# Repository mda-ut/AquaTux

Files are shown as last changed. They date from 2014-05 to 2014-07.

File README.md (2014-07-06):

AquaTux

Repository for University of Toronto's Mechatronics Design Association, which houses all revision controlled software and hardware for our team's entry into the international RoboSub competition: AquaTux!

See http://www.auvsifoundation.org/foundation/competitions/robosub/ for more detail on the competition. Also, our non revision controlled resources can be found at: https://www.dropbox.com/sh/x1nmdbmocld3edr/AAAKEdywBxVcvkEa93l7Mutga. See http://mda.markharfouche.com for our wiki, which is helpful for getting started with this repo.

Happy swimming!

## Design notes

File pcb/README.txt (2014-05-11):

Directory: root
Use: Should hold all the MDA PCB projects
Author: Mark Harfouche
Editors:

Every unique board should have it's own directory.
Updated revisions of an existing board should be kept in originals directory. 

Unlike what Mark had previously stated. We support both EAGLE and ALTIUM for PCB development. Pick your poison. 

Do not commit generated files such as Gerbers unless they are final revisions. 

-- David Biancolin (Dec, 2012)

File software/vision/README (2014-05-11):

This is the second iteration in writing a good vision code system.
Main Goals
  - Seperation of layers of code:
    - img/filter layer, task layer, mission layer
  - Use .msf text files to store configuration info
  - Better interface between vision and control
  - Minimize explicit use of opencv in main functions

Important Things:
  - You need a "common_settings.msf" in settings, which contains the minimum
    needed config info to start the system. This is extensively hardcoded
  - Each filter and task has its own settings file
  - In a settings file, any setting that looks like _LENGTH_ will be a scale
    factor from zero to 1. In the code this ratio is multiplied by an
    appropriate value indicated in the comments. 
  - A setting like LENGTH without underscores will behave as the value itself.
  - Use "gtk-v4l" to edit hardware camera settings
    - (or v4l2ucp on the netbook)

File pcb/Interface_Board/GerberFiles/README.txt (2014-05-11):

Board: InterfaceBoard
Date: 2012-02-12
Designer: Jordan Varley
Board Dimensions: 6.000 x 4.000 inches

List of Files:
--------------
*.drd   Excellon drill description
*.dri   Excellon drill tool description
*.cmp   Component (top) side copper
*.sol   Solder (bottom) side copper
*.plc   Component (top) side silk screen data (includes board outline)
*.stc   Component (top) side solder stop mask data
*.sts   Solder (bottom) side solder stop mask data
*.gpi	Gerber photoplotter information data

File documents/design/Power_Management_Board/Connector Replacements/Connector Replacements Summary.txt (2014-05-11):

%%%%%%%%%%%%%%%%%%%%%%%%%%%%%%%%%%%%%%%%%%%%%%
%              Power Connectors              %
%%%%%%%%%%%%%%%%%%%%%%%%%%%%%%%%%%%%%%%%%%%%%%

5-pin Power Connector
---------------------
HEADER
 Manufacturer    = Hirose Electric Co Ltd
 Manufacturer PN = DF5A-5P-5DSA(05)
 Digikey PN      = H10284-ND

CONNECTOR
 Manufacturer    = Hirose Electric Co Ltd
 Manufacturer PN = DF5A-5S-5C
 Digikey PN      = H1903-ND

3-pin Power Connector
---------------------
HEADER
 Manufacturer    = Hirose Electric Co Ltd
 Manufacturer PN = DF5A-3P-5DSA(05)
 Digikey PN      = H10282-ND

CONNECTOR
 Manufacturer    = Hirose Electric Co Ltd
 Manufacturer PN = DF5A-3S-5C
 Digikey PN      = H1901-ND

2-pin Power Connector
---------------------
HEADER
 Manufacturer    = Hirose Electric Co Ltd
 Manufacturer PN = DF5A-2P-5DSA(05)
 Digikey PN      = H10281-ND

CONNECTOR
 Manufacturer    = Hirose Electric Co Ltd
 Manufacturer PN = DF5A-2S-5C
 Digikey PN      = H1900-ND

Crimp Contacts
--------------
 Manufacturer    = Hirose Electric Co Ltd
 Manufacturer PN = DF5A-1822SCF(51)
 Digikey PN      = H1933CT-ND
 Wire AWG        = 18-22
 Jacket Diameter = 2.2-3.2mm

%%%%%%%%%%%%%%%%%%%%%%%%%%%%%%%%%%%%%%%%%%%%%%
%       FPGA-PowerManagement Connector       %
%%%%%%%%%%%%%%%%%%%%%%%%%%%%%%%%%%%%%%%%%%%%%%
HEADER
 Manufacturer    = TE Connectivity
 Manufacturer PN = 5103309-1
 Digikey PN      = A33160-ND
 Pitch           = 0.100
 Row Spacing     = 0.100

CONNECTOR
 Manufacturer    = TE Connectivity
 Manufacturer PN = 1658527-3
 Digikey PN      = 1658527-3-ND
 Pitch           = 0.100
 Row Spacing     = 0.100

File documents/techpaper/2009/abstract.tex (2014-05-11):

%In the context of the AUVSI and ONR's Xth International Autonomous
%Underwater Vehicle Competition, the team at the University of Toronto
%built an underwater vehicle.

AquaTux is the third entry of the University of Toronto Mechatronics
Design Association into the annual Autonomous Underwater Vehicle
Competition.  The vehicle is designed to autonomously complete
the set of tasks described in the mission\footnotemark[1]. It is
equipped with a passive sonar system, a compass, a depth sensor and two cameras that allow it to navigate in its environment. This
year's frame was built from the ground up based on the experience
acquired from past entries and is much more adapted to the underwater
conditions and the rigors of the competition. Along with the frame, we are
proud to present a new power system and more reliable electronics and
embedded communication protocols.

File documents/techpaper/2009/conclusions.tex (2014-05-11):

\section{Conclusions} 
\vspace{-.03in}

This year's team took on the challenge of building a completely new
autonomous underwater vehicle: AquaTux. This AUV is composed of an embedded
computer that is linked to an interconnection of microcontrollers. More emphasis was directed towards the frame to
ensure that the electronics remain dry. While a lot of the design
decisions are influence by our past experience, we also learned many
techniques and principles over the last year. Circuit board
fabrication, plastic machining and software engineering are some of
the skills that many of our members were able to acquire. More
rational design techniques and project management skills are also
derived from the our previous competitions and they had a significant
effect on maximizing the productivity of all the man-hours contributed
to the project.

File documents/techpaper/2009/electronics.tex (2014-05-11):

%\section{Electrical aspects}

\section{Electronics and Communication}
Our electronics were designed to handle all low-level tasks that are
required to move AquaTux, acquire sensor data and trigger
electrical systems like the  marker droppers. The main goal
of the electronics is to allow the AUV to be driven with only
high-level heading and depth commands. The electronics are responsible for
executing the commands and controlling their results (e.g. depth or
heading) in a ``black box'' fashion. This level of separation, created by our command
communication protocol, provides the option of tethered communication directly to the Navigation board via RS232 or through the computer's ethernet port
that relays commands to the Navigation board.

\subsection{Navigation Board}
The Navigation Board provides signal conditioning and circuitry interfacing for all sensors, including the Motor Boards and Peripheral Control Boards. In addition, all communication either goes to or through the navigation board. This is also
the access point when the computer has to communicate with the lower level
electronics. It features an LPC2129 microcontroller (MCU) at its core, operating at
12Mhz and utilizes Control Area Network (CAN), two-wire serial I2C,
and RS232 protocols to communicate with the Motor Boards, Peripheral
Control Board / Batteries, and the Computer respectively. The
navigation board reads the heading from an HMR3300 Digital Compass
connected through a serial port.  An analog pressure sensor, MPX4115, provides a linear
voltage representation of the depth, and is also connected to the
navigation board feeding directly into a successive approximation A/D
in the LPC2129. This board is the key element in handling all low-level operations such as movement and data collection.

\subsection{Peripheral Control Board}

The circuit board operates as an extension to the navigation board by
performing the tasks of actuating the marker droppers and debouncing
the custom-made leak sensors. The Peripheral Control Board uses
SN754410 quadruple half H-Bridge drivers: two of which are used to
actuate the marker droppers and one to fire the torpedo. The
Peripheral Control Board uses an ATmega48p MCU to control the half
H-bridge drivers, and query the leak sensors and the feedback switches
from the marker dropper. The microcontroller communicates with the
navigation board through the I2C network of the AUV.

\subsection{Motor Board}

The motor drivers are used to control the Seabotix BTD150 Thrusters
used on AquaTux.  There are a total of five motor drivers, one for
each thruster used on the AUV (Figure~\ref{mstack}). The motor drivers are based around the NXP
LPC2129 MCU which has number of features ideally suited to our
application, including a 4 channel SAR ADC, a 6-channel dual edge
triggered PWM module, a CAN module and a simple serial boot-loader.
The thrusters are controlled via current control, and other safety
features such as current limiting, and acceleration control are
implemented.  By receiving commands through the CAN bus, these Motor
Boards will ensure that the thrusters are never harmed by excessive
current during operation.

\begin{figure}
\begin{center}
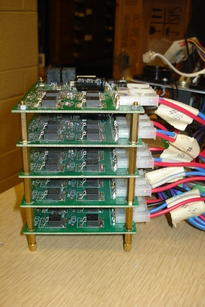
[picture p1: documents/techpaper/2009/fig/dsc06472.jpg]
  %1.34
\vspace{.05in}
\hrule
\caption{Stack of motor control boards on a CAN bus.}\label{mstack}
\end{center}
\end{figure}

The motor controller hardware is centered around a pair of Linear
Technology LT1160 half-bridge drivers which include high side charge
pumps, shoot through protection and undervoltage lockout. A number of
additional components were added to increase the bridge robustness
including TVS diodes, anti-parallel gate diodes and large on-board
bulk capacitors. Two types of sensors were integrated into the motor
board in order to sense motor function. Back EMF measurement
capability as well as motor current circuits were added. An active-RC
filter similar to that on the navigation board was used coupled with a
high side sense resistor and INA168 to measure the motor current.
Motor current measurement is critical as it must be kept below 4A to
prevent motor damage.

\section{Power Distribution}
AquaTux is powered by three 24V NiMH battery packs.  The three battery
packs each power a different section of the AUV.  Two packs directly
feed into the Motor Boards: one pack is used to power the three
vertical thrusters, and a second pack provides power for the two
horizontal thrusters.  The last battery pack provides power for the
rest of AquaTux after being conditioned by Switch Mode Power Supplies
(SMPS) to create two separate bus voltages. A 5V SMPS feeds the
Kontron SpeedMopsLcdPM PC104+ computer, while a 12V SMPS provides power to
all other modules of the AUV, which includes the navigation board,
cameras, and all other sensors. If other voltages are required for the
electronics, linear regulators are used to produce them.  In case of
emergency, relays toggled by magnetic switches are used to disconnect
the batteries from the rest of the AUV. Circuit breakers are also put
inline with the battery to act as both the fuse, and the power
switches for the AUV. The power architecture was designed to keep
board to board wiring simple by minimizing the number of bus voltages.

\subsection{Power Source}
The NiMH battery packs were custom designed by our team: each pack is
composed of 20 SY136T Sanyo nickel metal hydride batteries.  All
batteries are connected in series to form a 24V nominal battery pack
with a capacity of 4100mAh.  Each pack has its own protection
circuitry that utilizes an Atmega48p AVR as its MCU.  A gas gauging IC, BQ2013,
from Texas Instruments is used to track the charge status of the
battery. %BQ2013
For safety, the pack has a disconnect FET on the high side of the
battery.  This FET will disconnect the pack when the pack is drained
or at a temperature greater than 80 degrees Celsius. All battery packs
are connected to the I2C bus on the navigation board, allowing for
remote monitoring of the batteries at all time.

\subsection{Battery Charger}
The battery charger was also designed by our team and has at its core
an Atmega168p MCU.  This MCU monitors the voltage and
temperature of the battery pack being charged, and will automatically
terminate charging based on the temperature rise of the NiMH cells.
The charger must also communicate with the pack via I2C in order to
read the battery pack ID, and to ensure that the disconnect FET is
enabled for charging.  Charge current is set by utilizing a sense
resistor, and an opamp to control the gate voltage of a MOSFET.  The
MOSFET operates in saturation in order for us to appropriately limit
the charge current of the batteries. Because the voltage range of the
NiMH cells extends from 1.4V to 1.6V, the voltage supply required to
charge a 20 cell pack must be greater than 32V: we chose a 36V supply for cost-effectiveness.

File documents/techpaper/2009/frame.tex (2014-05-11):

\section{Frame design and construction}
The 2009 frame design underwent a complete revision based on our
experience from previous years.  Our past frame designs included
custom ordered molded or rapid prototyped parts intended to improve
the hydrodynamics of the hull.  After analyzing the conditions that
the vehicle would be subjected to, it was determined that the effects
of fluid dynamics were negligible in terms of functionality.  For this
reason, a ``design for manufacturing'' development methodology was
adopted: in efforts to minimize cost and machining time, the frame has been
designed to take advantage of commercial off-the-shelf parts as
well as capitalize on simple manufacturing processes.

\subsection{Design Considerations}
\label{fobjectives}
The design objectives in the 2009 frame were significantly more
ambitious as our team included more members adept in manufacturing.
The final concept was conceived such that it could be fabricated
without the need for outsourcing.

Below is the list of the desirable attributes for the frame that we set out to
obtain based on the experience gained from past frame designs:
\begin{packed_enum}
\item Minimize time required to access batteries and electronics;
\item Maximize modularity for easier transport and progressive revisions;
\item Optimize mass for transport, functionality and points;
\item Provide a secure removable internal rack for electronics to facilitate bench testing;
\item Obtain a a waterproof seal with a simple low tolerance assembly;
\item Create solid harness points and handles;
\item Facilitate movement through water and maximize battery life with
  a neutrally buoyant design;
\item Compensate for changes in mass distribution and motion
  calibration with adjustable thruster positions;
\item Design an attractive and professional looking vehicle.
\end{packed_enum}

\subsection{Frame Overview}
The AquaTux frame design can be divided into three
subsections: external frame, hull, and internal rack.  The goals based
on past experience described above suggested the need to
minimize the number of sealing surfaces and reduce the number of
waterproof connectors.  To achieve these objectives, a single enclosure
was created (the hull) to encapsulate everything except for the
markers to be dropped, the thrusters and the hydrophones.  These external components would be
connected to an exoskeleton type frame which allows for flexible
mounting arrangements.  Finally an internal rack was designed to hold
 all the electrical components including cameras and embedded computer.

\subsubsection{External Frame}
The external frame was designed with transportation and fabrication as
the primary constraints. This exoskeleton is made entirely of
commercial off-the-shelf
parts, $\frac{1}{2}$ inch PVC plumbing pipe and connectors.  The thruster positions
are fully adjustable since they are attached to individual pipes fixed
in place by standard gear clamps (Figure~\ref{adj}). The adjustability of the frame also
facilitates transportation as the entire structure can be collapsed to
fit a smaller envelope. 

\begin{figure}
\begin{center}
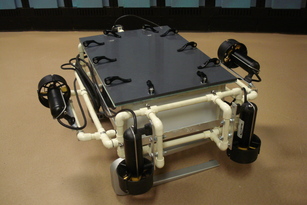
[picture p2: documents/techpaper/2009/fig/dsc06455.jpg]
  
% \includegraphics[width=3in]{fig/dsc06453} 
\vspace{.05in}
\hrule
\caption{Adjustable PVC tube exoskeleton frame.}\label{adj}
\end{center}
\end{figure}

In order to ensure a simple assembly method and utilize standard
connectors, the mechanism for picking up the briefcase was made of the
same material as the external frame.  It utilizes the fact that the
target is an open-walled structure and consists of a fork designed to
spear the case so that it can surface with the vehicle.

\subsubsection{Hull}
This year's hull design attempts to minimize the number of sealing
surfaces while maintaining usable space inside the vehicle.  In order
to seal the hull, a lid was made with a special simplified o-ring
groove (Figure~\ref{oring}). To avoid the need for precision milling or numerically
controlled machines, an oversized rectangular groove was cut.  The
corners were then drilled out and replaced with nylon dowels to
prevent the sharp corners from cutting into the o-ring.  This design
eliminated the need for specialized end mills or the need to mill
curved patterns in the lid. 

\begin{figure}
\begin{center}
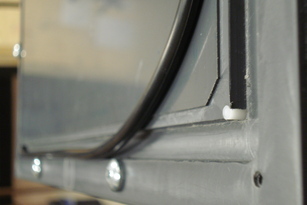
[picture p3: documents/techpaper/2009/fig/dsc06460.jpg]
  
\vspace{.05in}
\hrule
\caption{O-ring displaced to show the grooves and nylon dowel.}\label{oring}
\end{center}
\end{figure}

Past experience suggested the need for a quicker method to access the
internal components of the hull.  Quick-release latches 
(Figure~\ref{quick}), were
used to replace nuts and bolts which take significantly more time to
release.  These latches use a cam mechanism to clamp the lid to
metallic bars and subsequently compress the o-ring, creating a water-tight seal.

\begin{figure}
\begin{center}
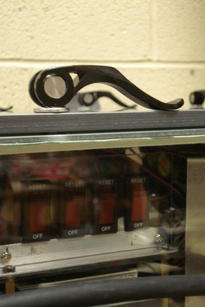
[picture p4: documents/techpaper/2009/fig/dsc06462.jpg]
  
\vspace{.05in}
\hrule
\caption{Quick release cover mechanism.}\label{quick}
\end{center}
\end{figure}

An endplate was designed to provide a single replaceable surface to accept all the connectors between the interior and exterior of the vehicle.  This endplate is sealed with a groove similar to that of the lid and is attached with self sealing screws from APM Hexseal.  The waterproof connectors which pass through the endplate lead to two master-disconnects which allow for quick and easy installation of the internal rack (Figure~\ref{endplate}).
The waterproof connectors chosen are 8-pin Neoprene molded connectors
from Impulse Enterprise.  These connect the thrusters as well as the
wireless tether and provide maximal flexibility due to their pin count
as well as small profile.  
The pressure readings for the AUV are also gathered  through the
endplate. In order to sense depth, a MPX4115 pressure transducer is
coupled to a segment of PVC tubing connected to a compression nut on
the endplate.  The depth of the vehicle corresponds to the pressure of
the air trapped in the PVC tubing.
  The hull is fabricated from
$\frac{1}{8}$ inch thick polycarbonate sheets, with waterproof epoxy bonding
the joints together.  To strengthen the bonds, aluminum angle brackets
were added to the edges to increase the bonding area of the epoxy. The thin, clear polycarbonate walls of the hull allow subsystems such as the cameras, marker droppers (section~\ref{mdroppers}) and trigger for the torpedo to operate from within the vessel.

\begin{figure}
\begin{center}
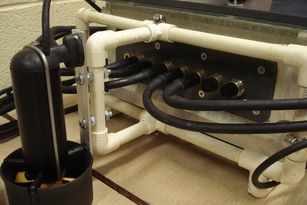
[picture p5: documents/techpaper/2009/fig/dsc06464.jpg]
\subfigure[Endplate showing waterproof connectors.]{  }
\subfigure[Master disconnects for the waterproof connectors on the
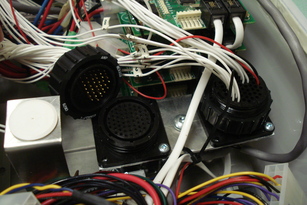
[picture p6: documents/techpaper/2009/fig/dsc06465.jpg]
inside of the vehicle.]{  }
\vspace{.05in}
\hrule
\caption{Connection system to the outside of the vehicle.}\label{endplate}
\end{center}
\end{figure}

\subsubsection{Internal Rack}
In addition to remedying problems with our previous frames, we
endeavored to produce a frame that could be reconfigured and usable in
future years.  The concept for the internal rack (Figure~\ref{rack})
consists of base plates that accepts stacks of electronics.  These
plates can be removed as a single unit which facilitates wiring, and
bench testing.  Due to the buoyancy of the hull, stainless steel bars
were used to add weight to the vehicle (Figure~\ref{rack}).  These weights act as a method of balancing the
vessel and allow the electrical components to be reconfigured for
years to come.  The internal rack does not rest directly on the floor
of the hull.  In case of a leak, water would collect in the space
below the electrical components and be detected with leak sensors
prior to any damage.

\begin{figure}
\begin{center}
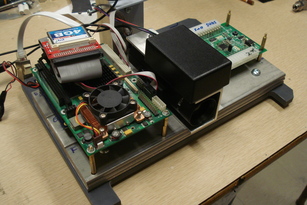
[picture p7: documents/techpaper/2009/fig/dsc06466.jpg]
  
\vspace{.05in}
\hrule
\caption{Inside rack holding the electronics and the stainless steel weights.}\label{rack}
\end{center}
\end{figure}

\section{The Marker Dropper}
\label{mdroppers}

The thin walls of the hull facilitate the operation of a simple marker dropper system which
can be centered around the downward facing camera.  Two ferrous
markers are placed on the exterior of the vessel and held in place by
a magnetic attraction to two rare earth magnets located on the inside
of the hull.  The magnets are connected to individual stepper motors
which retract the magnets from the wall of the hull (Figure~\ref{md2}).  The increased
distance between the magnets and the markers causes a reduction in
magnetic field strength allowing the markers to drop freely from the
vehicle.

\begin{figure}
\begin{center}
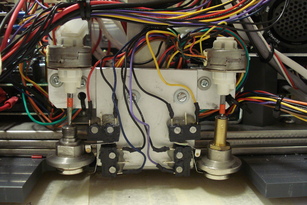
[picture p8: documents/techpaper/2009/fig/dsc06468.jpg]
  
\vspace{.05in}
\hrule
\caption{Two marker-droppers: from top to bottom, a stepper motor
  retracts a magnet from the surface of the hull (bottom in the figure).}\label{md2}
\end{center}
\end{figure}

\section{The Torpedo Launcher}
\label{torpedo}
\vspace{-.1in}
One of the primary goals of this year's entry into the AUV Competition
was to minimize the number of connections that pass through the
endplate of the hull.  The resulting design for a torpedo launcher was
an external system that was activated by a magnetic switch.  This
concept allowed us to mimic the marker dropper design to activate the
torpedo.  The external system  contains only a few simple parts; a
power supply (9V battery), a solenoid valve, a magnetic switch, a
compressed gas cylinder and a projectile. As the magnet in the hull
is retracted from the hull, the magnetic switch is
triggered.  The switch  then triggers the solenoid valve allowing
compressed gas to fire the torpedo.

The controls for the above mentioned systems are described in the
following sections.

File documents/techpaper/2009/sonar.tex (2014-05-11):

\section{Passive Sonar}

The sonar subsystem was designed to localize an underwater acoustic beacon emitting at a specific frequency, interpret the tones that it produces and identify the position of the beacon relative to that of the submersible.

\subsection{Principles utilized}

The concept behind passive localization is the detection of "Time
Delays on Arrival" (TDoA) between multiple receivers in a known
geometric configuration. A set of $n$ receivers will produce $n-1$
TDoA values, i.e. one between a reference receiver and every other
receiver in the array.

This concept has limitations: in a 2D (planar) environment, at least
three receivers are required to produce a location. In this case, each
TDoA value, when coupled with the receiver position produces a
hyperbola of possible solutions. To find a point solution, two
TDoA/geometry pairs must be used, and the intersection of the two
resulting hyperbolas calculated. In three dimensions, four receivers
must be used (producing a total of three TDoA values.) This is due to
the fact that each TDoA value/receiver geometry pair produces a
hyperboloid of possible solutions. The intersection of three
hyperboloid surfaces will produce the transmitter location in
question.

Although a closed form solutions exist for both the two and
three-dimensional cases, they are difficult to implement numerically.
To counter this problem, several methods of approximation and
simplification exist: we decided to focus Carter's method\footnote{C. Carter,
  Time Delay Estimation for Passive Signal Processing, IEEE
  Transactions on Acoustics, Speech and Signal Processing, Vol.
  ASSP-29, No.3, 1981, pp. 463-470.}. Carter's method uses the
approximation that the distance between receivers is much smaller than
the distance from receivers to source to approximate the distance and
heading of the beacon in two dimensions. This solution is simple and
holds in a large variety of conditions, making it an ideal candidate
for implementation.

\begin{figure}
  \hrule
  \vspace{.05in}
\centering
\subfigure[Simulated signal perceived by the hydrophones with random noise, echoes and ground references.] {
  
  \label{fig:bypass_cad}
}
\subfigure[Smoothed and rectified signals before edge detection and correlation.] {
  
  \label{fig:bypass_eff}
}
  \vspace{.05in}
\hrule
\caption{Examples artificial signals used to experiment with our
  algorithm. The 'x' axis is time and the 'y' axis is amplitude (in
  units matching the intensity of the received signal).}  \label{waves}
\end{figure}

The TDoA method of localization depends very heavily on the accuracy
and precision of the determination of time of arrival of the ping: the time of arrival between the
hydrophones represents a small number of audio samples. This is a
significant challenge when noise and A/D conversion and environment
limitations must be robustly handled. To determine the TDoA of 2
signals, we detect the arriving edge of the ping then improve the
accuracy of our estimation by cross-correlating the two signals (Figure~\ref{waves}).
Cross-correlation  measures the similarity of two
signals. Given two discrete signals $g(n)$ and $h(n)$, the
cross-correlation function $x(d)$ is:

\begin{equation}
x(d) = \sum( g(n)*h(n-d) )
\end{equation}

where $d$ is a phase shift introduced in one of the signals. The
cross-correlation $\sum x(d)$ is then a function of $d$, and is
maximized when the phase-shifted signal $h(n-d)$ matches the signal
$g(n)$ most closely.  To determine the time delay $d$ between signals
from two receivers, the cross-correlation of the two signals is
performed over a range of probable $d$ values.

\subsection{Implementation}
The sonar system was designed to exploit the ample processing power
and familiar debugging environment available  within the main
computer of the AUV. The analog sonar
system consists of two parts: a pre-amplifier with a high
impedance input  followed by
a  filtering and gain stage. The circuit was
specially designed for single supply operation to limit the complexity
of the power supply required.  A dsPIC30F4013 is used to
simultaneously sample and buffer the outputs of the analog stage. The
data is then fed to the main computer using an RS-232 serial interface
for high-level processing and decision making.

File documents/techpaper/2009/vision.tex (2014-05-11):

\section{Machine Vision }

The vision subsystem is a critical component of AquaTux because it is
the one performing the identification of mission objectives. It is
also complementary to the passive sonar to grab the suitcase above the
acoustic pinger. Because the turbidity of the water and the small
number of visual features in the underwater floor prevent making
reliable correspondences between two views, we decided that stereo
vision was impractical in our vessel. Instead, we use two independent
cameras: one facing forward and one facing down. Since they
are rigidly attached to the AUV, we need to move the AUV
to change the viewpoint. In this section, we explain in more details
the features of our vision subsystem.

\subsection{Vision Hardware}
The vision hardware consists of two low light color cameras based
around $\frac{1}{3}$ inch Sony CCD sensors: these cameras were selected for their
image quality in low light situations, small size and price. Standard
adjustable lenses were used on each camera for maximum flexibility. A
Sensoray 311 capture card performs the video capture and frame
acquisition and communicates with our embedded computer through the
compact PC-104+ bus. The card provides 4 input channels at capture
rates up to 30 frames per second (fps). The computer does not sample
images at regular intervals: the actual frame rate depends on the
amount of processing required for a particular image, which will vary
depending on the task. The on-board computer was chosen to ensure that
it is fast enough to achieve a processing frame rate of at least 10
fps.  While we initially selected a Blackfin DSP to do the task, we
later decided to upgrade to a full-featured embedded Pentium 4 1.8Ghz
computer. This computer is equipped with an Ethernet port allowing to
connect to the wireless tether.

\subsection{Software Organization}
\label{gui}

\begin{figure}
\begin{center}
 
\caption{Vision modules organization in the AUV.}\label{vision}
\end{center}
\end{figure}

\begin{figure}
\begin{center}
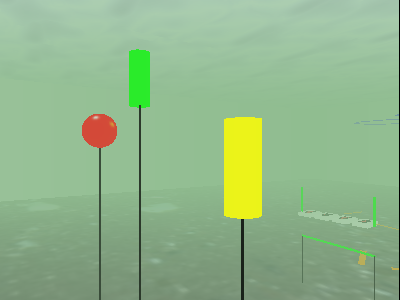
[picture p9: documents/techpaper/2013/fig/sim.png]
 
\caption{Example image from the simulator showing pipe segments, a box
  and a red buoy in turbid water.}\label{sim}
\end{center}
\end{figure}

The vision system is broken down in 3
software components (Figure~\ref{vision}): (i) the mission software that performs the image
processing; (ii) the simulator that recreates synthetic underwater
images based on the vehicle position (example in
Figure~\ref{sim}) and (iii) the graphical interface that is used to
control the mission software. The simulator and the graphical
interface were solely created to test and debug the vision
algorithms when AquaTux is not functioning autonomously. All modules connect through TCP/IP in a
very flexible and extensible fashion. This allows us to seamlessly
replace the simulator by the real hardware sensors and electronics
when we take our system from the lab to the water environment. The
graphical interface allows us to access all the data structures in the
AUV and can act as a passive observer, constantly requesting the
state of the vehicle, or as a controller sending commands to the
vessel.

\vspace{-.1in}
\subsection{Image Processing Software}
The image processing software consists of color filters and edge and
line detection algorithms. The color filters allow us to select
specific information to only process relevant parts of the images. The
line processing algorithms use heuristics to form polygons and
recognize objects such as pipes or boxes, that have a well defined
appearance. Our algorithms are robust enough to recognize objects even
if their view changes due to perspective or the presence of debris in
the water.  The mission software consists of a main loop that acquires
images, processes them and send commands to the other subsystems on
one of the two serial ports of the embedded computer (see
Section~\ref{gui}). The mission is broken down into modular tasks that
can me chained or tested individually. Tasks proceed by first
identifying a target for the vehicle to begin pursuit. If the object
in question is not found, the vehicle rotates on its vertical axis
(yaw) to make the cameras pan to the right and to the left. If nothing
is found, then the vehicle proceeds forward in its initial direction.
Once a target is acquired, the vertical position and lateral positions
of the vessel are controlled to match the desired coordinates.  The
vehicle uses a combination of heading relative to its current
orientation and absolute headings (relative to the magnetic north
pole) to navigate inside the environment. This alleviates the need to
get real-time measurements of the heading as the vehicle is
navigating. A limitation of our vision hardware that we had to address
is to determine when a task is completed if the view of the target is
obscured or occluded due to the AUV's proximity (e.g. it is passing
under the gate). In such situations, for the moment being, we use
timers to ensure that the vehicle reaches its target location.

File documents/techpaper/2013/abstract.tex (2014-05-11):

%In the context of the AUVSI and ONR's Xth International Autonomous
%Underwater Vehicle Competition, the team at the University of Toronto
%built an underwater vehicle.

AquaTux is the fourth entry of the University of Toronto Mechatronics
Design Association into the annual Autonomous Underwater Vehicle
Competition.  The vehicle is designed to autonomously complete
the set of tasks described in the mission\footnotemark[1].
It is equipped with an IMU, a depth sensor,
and two cameras that allow it to navigate in its environment.
This year's frame was reused from previous years.
We are proud to present new electronics, a new power system,
a new embedded system using an FPGA, and new software.

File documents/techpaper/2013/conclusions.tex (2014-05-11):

\section{Conclusions} 
\vspace{-.03in}

This year's team took on the challenge of building all of Aquatux's electronics
and software within the existing frame. This AUV is composed of a Netbook that
is linked to a single FPGA that drives the electronic peripherals.
The Netbook runs mission-aware vision software, which uses the OpenCV library.
Circuit board fabrication, plastic machining, embedded programming,
and software engineering are some
of the skills that many of our members were able to acquire. More
rational design techniques and project management skills are also
derived from the our previous competitions and they had a significant
effect on maximizing the productivity of all the man-hours contributed
to the project.

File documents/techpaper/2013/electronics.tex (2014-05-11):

%\section{Electrical aspects}

\section{Electronics}
Our electronics were designed to handle all low-level tasks that are
required to move AquaTux, acquire sensor data from the IMU and depth sensors. 
The main goal of the electronics is to allow the AUV to be driven with only
high-level heading and depth commands. The electronics are responsible for
executing the commands and controlling their results (e.g. depth or
heading) in a ``black box'' fashion. The electronics are managed by the embedded
system described in the next section, giving access to each electronic peripheral.

Aquatux's electronics are arranged in two stacks of PCBs, one dedicated to power 
distribution and management, and the ``main stack'', which breaks out the on board 
FPGA's I/Os to any number of children.

\subsection{Main Stack}
At the heart of Aquatux's electronic subsystem is a Terasic DE0-Nano, a small 
form-factor FPGA development board, containing an Altera Cyclone IV FPGA. The 
DE0 mates directly to the ``Interface Board'' which breaks out all of the 
available I/0s to a 120 pin board to board connector (Figure~\ref{mstack}). Any number of new PCBs 
can be mated, by providing the mating male and female connectors. These 
connectors form a wide bus between the FPGA and the mating boards, which when 
coupled with the reconfigurability of an FPGA, makes it very easy to incorporate 
new PCBs without having to physically rewire parts of the submarine -- a Quartus 
recompile is all that's required. The interface board also connects to the IMU, 
a VectorNav VN-100 Rugged, which performs its own sensor signal processing to 
output attitude data to the FPGA.

\begin{figure}
\begin{center}
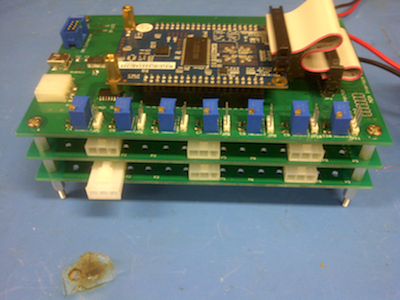
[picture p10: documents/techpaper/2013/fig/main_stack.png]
  %1.34
\vspace{.05in}
\hrule
\caption{The main stack connector. Top, the interface board and DE0 nano. Below, two 6 channel motor drivers.}\label{mstack}
\end{center}
\end{figure}

\subsection{Motor Board}

The motor boards are used to control the Seabotix BTD150 Thrusters used on AquaTux 
and other actuators internal to the submarine. Each motor board (Figure~\ref{motorb}) consists of 6 NMOS 
high-side half bridges driven by Linear Technologies LT1660 half-bridge drivers. 
Each half bridge has a sister with which it can be used a full bridge, by soldering 
the output connector in the correct position. Complementary PWM inputs to each driver 
can be sourced from one of three sets of I/Os provided via the main stack connector, 
allowing a multiplicity of boards to be mated to the stack. Presently, two of three 
boards are used, providing the five full bridges required to drive Aquatux's motors. 
The final board is provision to drive internal peripherals such as marker droppers in 
future competitions.

\begin{figure}
\begin{center}
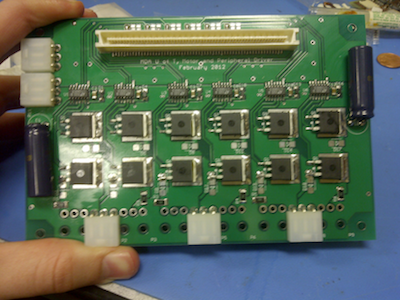
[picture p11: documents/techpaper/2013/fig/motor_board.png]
  %1.34
\vspace{.05in}
\hrule
\caption{A motor board, configured with 3 full bridges.}\label{motorb}
\end{center}
\end{figure}

\subsection{Power Distribution}
Power for Aquatux's electronic systems, excluding the netbook, is provided by 
two 24V NiMH battery packs. The power distribution board switches the battery 
voltage with a relay, which is controlled by the FPGA's soft-processor. 
Throwing the kill switch (by removing the velcroed handle on the side of the 
hull) opens a reed switch which breaks the relay's coil current. Three DC/DC 
converters (3.3V, 5V, 12V) source from this voltage, and form a stack of PCBs 
with the power management board above them. LC output filters on power management 
board remove switching harmonics, before breaking out the rail voltages to the 
submarine through a series of copper bus-bars. Four pairs of analog comparators 
alert the FPGA when any of the rails over or under-volts by 5 percent of their nominal 
voltage. As a final baseline precaution, breakers have been inserted between the 
batteries and relay, and between the power management board and bus-bars for each rail.

\subsection{Power Source}
The NiMH battery packs were custom designed by our team: each pack is
composed of 20 SY136T Sanyo nickel metal hydride batteries. All
batteries are connected in series to form a 24V nominal battery pack
with a capacity of 4100mAh. Temperature sensors embedded in each pack allow 
the FPGA to kill the sub if any one pack overheats.

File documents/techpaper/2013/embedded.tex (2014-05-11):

\section{Embedded System}

The embedded system was designed to link the submarine's computer with all
electronic peripherals, with a high-level interface to access groups of peripherals.
The embedded system consists of a DE0-Nano FPGA, synthesizing custom circuitry to
communicate with each peripheral and a soft processor to communicate with the computer. The FPGA was chosen
for its quantity of general-purpose I/O pins, allowing it to manage all electronic peripherals,
and its compact size of 3x2 inches. The FPGA is the only programmable element in the submarine
besides the computer, reducing the amount of communication between programmable elements.

\subsection{FPGA Soft Processor}

The FPGA Soft Processor exposes high-level commands to the computer to access each group
of electronic peripherals.
The IMU and depth sensor provide attitude readings and are used by the PID controllers and the
computer interface. Power management continually monitors each
voltage rail, and will power off the submarine if any voltage is invalid.
The five motor drivers are controlled together by the soft processor's yaw, pitch, roll,
and depth PID controllers. The computer interface can set target
speed, yaw, and depth, which are inputs to the PID controllers. Speed is implemented as an offset
because the submarine does not have velocity measurement. The PID controllers are implemented on the
soft processor because they need immediate access to the motor drivers and attitude readings.
The high-level commands are
text-based, allowing manual control to test each peripheral individually.
Future plans for sonar processing will be implemented on the FPGA, using the soft processor and
built-in DSP elements.

\subsection{FPGA Hardware}

The FPGA also synthesizes custom hardware to communicate with peripherals through general-purpose pins.
This flexibility can support any protocol to communicate with peripherals, including SPI and UART.
Each peripheral protocol is a separate module, memory-mapped to the soft processor across Altera's
Avalon Bus. The DE0-Nano has 85 general-purpose pins for digital inputs and 8 ADC inputs.
The depth sensor is an analog peripheral, and all other peripherals communicate digitally.
The hardware and soft processor run at 50 MHz.

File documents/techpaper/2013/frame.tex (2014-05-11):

\section{Frame design and construction}
The current frame design is mostly unchanged from previous years.
Under the vehicle's operating conditions, we determined that the effects
of fluid dynamics were negligible in terms of functionality.  For this
reason, a ``design for manufacturing'' development methodology was
adopted: in efforts to minimize cost and machining time, the frame has been
designed to take advantage of commercial off-the-shelf parts as
well as capitalize on simple manufacturing processes.

\subsection{Design Considerations}
\label{fobjectives}
The final design was conceived such that it could be fabricated
without the need for outsourcing.

Below is the list of the desirable attributes for the frame that we set out to
obtain based on the experience gained from past frame designs:
\begin{packed_enum}
\item Minimize time required to access batteries and electronics;
\item Maximize modularity for easier transport and progressive revisions;
\item Optimize mass for transport, functionality and points;
\item Provide a secure removable internal rack for electronics to facilitate bench testing;
\item Obtain a a waterproof seal with a simple low tolerance assembly;
\item Create solid harness points and handles;
\item Facilitate movement through water and maximize battery life with
  a neutrally buoyant design;
\item Compensate for changes in mass distribution and motion
  calibration with adjustable thruster positions;
\item Design an attractive and professional looking vehicle.
\end{packed_enum}

\subsection{Frame Overview}
The AquaTux frame design can be divided into three
subsections: external frame, hull, and internal rack.  The goals based
on above suggested the need to
minimize the number of sealing surfaces and reduce the number of
waterproof connectors.  To achieve these objectives, a single enclosure
was created (the hull) to encapsulate everything except for the
markers to be dropped, the motor thrusters and the hydrophones.  These external components would be
connected to an exoskeleton type frame which allows for flexible
mounting arrangements.  Finally an internal rack was designed to hold
 all the electrical components including cameras and embedded computer.

\subsubsection{External Frame}
The external frame was designed with transportation and fabrication as
the primary constraints. This exoskeleton is made entirely of
commercial off-the-shelf
parts, $\frac{1}{2}$ inch PVC plumbing pipe and connectors.  The thruster positions
are fully adjustable since they are attached to individual pipes fixed
in place by standard gear clamps (Figure~\ref{adj}). The adjustability of the frame also
facilitates transportation as the entire structure can be collapsed to
fit a smaller envelope. 

\begin{figure}
\begin{center}
  
\vspace{.05in}
\hrule
\caption{Adjustable PVC tube exoskeleton frame.}\label{adj}
\end{center}
\end{figure}

In order to ensure a simple assembly method and utilize standard
connectors, the mechanism for picking up the briefcase was made of the
same material as the external frame.  It utilizes the fact that the
target is an open-walled structure and consists of a fork designed to
spear the case so that it can surface with the vehicle.

\subsubsection{Hull}
The hull design attempts to minimize the number of sealing
surfaces while maintaining usable space inside the vehicle.  In order
to seal the hull, a lid was made with a special simplified O-ring
groove (Figure~\ref{oring}). To avoid the need for precision milling or numerically
controlled machines, an oversized rectangular groove was cut.  The
corners were then drilled out and replaced with nylon dowels to
prevent the sharp corners from cutting into the O-ring.  This design
eliminated the need for specialized end mills or the need to mill
curved patterns in the lid. 

\begin{figure}
\begin{center}
  
\vspace{.05in}
\hrule
\caption{O-ring displaced to show the grooves and nylon dowel.}\label{oring}
\end{center}
\end{figure}

Past experience suggested the need for a quicker method to access the
internal components of the hull.  Quick-release latches 
(Figure~\ref{quick}), were
used to replace nuts and bolts which take significantly more time to
release.  These latches use a cam mechanism to clamp the lid to
metallic bars and subsequently compress the O-ring, creating a water-tight seal.

\begin{figure}
\begin{center}
  
\vspace{.05in}
\hrule
\caption{Quick release cover mechanism.}\label{quick}
\end{center}
\end{figure}

An endplate was designed to provide a single replaceable surface to accept all the connectors between the interior and exterior of the vehicle.  This endplate is sealed with a groove similar to that of the lid and is attached with self sealing screws from APM Hexseal.  The waterproof connectors which pass through the endplate lead to two master-disconnects which allow for quick and easy installation of the internal rack (Figure~\ref{endplate}).
The waterproof connectors chosen are 8-pin Neoprene molded connectors
from Impulse Enterprise.  These connect the thrusters as well as the
wireless tether and provide maximal flexibility due to their pin count
as well as small profile.  
The pressure readings for the AUV are also gathered  through the
endplate. In order to sense depth, a MPX4115 pressure transducer is
coupled to a segment of PVC tubing connected to a compression nut on
the endplate.  The depth of the vehicle corresponds to the pressure of
the air trapped in the PVC tubing.
  The hull is fabricated from
$\frac{1}{8}$ inch thick polycarbonate sheets, with waterproof epoxy bonding
the joints together.  To strengthen the bonds, aluminum angle brackets
were added to the edges to increase the bonding area of the epoxy. The thin, clear polycarbonate walls of the hull allow peripherals such as the cameras, marker droppers and torpedo trigger to operate from within the vessel.
Although the marker droppers and torpedo launcher did not make it into this
year's submarine, the polycarbonate walls facilitate the addition of the
peripherals and a method to actuate them.

\begin{figure}
\begin{center}
\subfigure[Endplate showing waterproof connectors.]{  }
\subfigure[Master disconnects for the waterproof connectors on the
inside of the vehicle.]{  }
\vspace{.05in}
\hrule
\caption{Connection system to the outside of the vehicle.}\label{endplate}
\end{center}
\end{figure}

\subsubsection{Internal Rack}
The frame was designed to be reconfigured and usable in
future years. The concept for the internal rack consists of base plates that 
accepts stacks of electronics.  These plates can be removed as a single unit which 
facilitates wiring, and bench testing.  Due to the buoyancy of the hull, 
stainless steel bars were used to add weight to the vehicle. These weights act as 
a method of balancing the vessel and allow the electrical components to be easily 
removed for debugging or modifications. The internal rack does not rest directly 
on the floor of the hull. In case of a leak, water would collect in the space
below the electrical components and be detected with leak sensors
prior to any damage.

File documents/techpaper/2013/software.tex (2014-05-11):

\section{Software}

The submarine's software is aware of the competition objectives, and performs computer vision to
command the submarine to move through the embedded system.
The software is organized so that it is easy to test the core vision and control systems with different
sources of video input and to command the submarine or the simulator to move.
The software also includes a graphical simulator that we can use to test our vision and control algorithms.

\subsection{Software Organization}
\label{gui}

\begin{figure}
\begin{center}
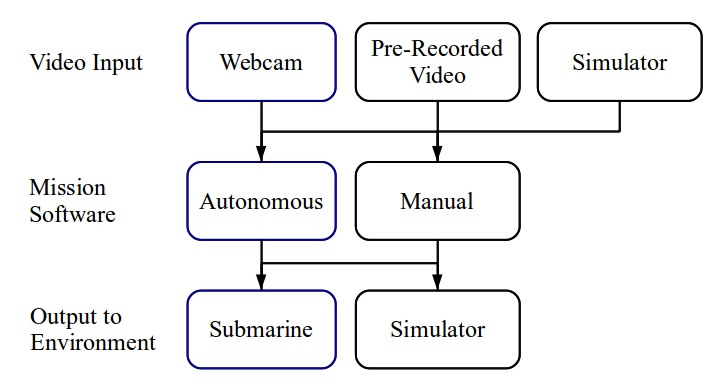
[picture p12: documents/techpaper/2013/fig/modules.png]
 
\caption{Software module organization.}\label{modules}
\end{center}
\end{figure}

\begin{figure}
\begin{center}
 
\caption{Example image from the simulator showing pipe segments and the buoys
         in turbid water.}\label{sim}
\end{center}
\end{figure}

The software is broken down into 3
components (Figure~\ref{modules}): (i) the video input;
(ii) the mission software gives physical commands to move the sub;
and (iii) the environment that reacts to the physical commands.
The video input can come from the submarine's webcams, pre-recorded video,
or the simulator (Figure~\ref{sim}). The mission software can be the autonomous
algorithms that drive the submarine or a manually controlled user interface.
The environment that reacts to physical commands can be the submarine or the
simulator. The different permutations to hook up the software components
solely created to test and debug the vision
algorithms when AquaTux is not functioning autonomously.
These software interfaces help ensure the software to test the submarine
resembles the autonomous functionality as much as possible.
The manual user interface allows us to act as a passive observer,
constantly requesting the state of the vehicle,
or as a controller sending commands to the AUV.

\subsection{Simulator}
The simulator is a piece of software written in C++ using the OpenGL library. Its purpose is to simulate the competition grounds so the software and vision algorithms can be tested with greater ease. The simulator was extremely useful, as using a pool is both expensive and time consuming.

The simulator contains a physical model of each obstacle in the competition,  as well as a method to track the locations of the two cameras on the sub. OpenGL calls are then used to draw the images that would be seen by the cameras, which are then extracted to the image processing algorithms (Figure~\ref{sim} shows an image that would be seen by the forward camera).
The simulator can accept commands to move the camera viewpoint, so that we can properly simulate video feedback when the submarine is commanded to move.

\subsection{Software Control}
Our control algorithms are run the submarine runs autonomously. The entire mission is broken down into tasks, such as the gate or buoy task,
which are implemented in separate modules. The control code queries the vision system for circles, lines or rectangles, and translates the
vision result into a movement command. While the submarine is reacting to a movement command, the video input is ignored to prevent
overshooting or oscillating the target.
Each control task can be tested separately.

\section{Vision}
The machine vision system is defined as all software and hardware which converts images (the input to the system) into numerical data (the output). This data refers primarily to the existence, position, orientation, and color of various objects in the image, such as the starting gate or a colored buoy. This information is handed off to the rest of the software, which acts on it to determine the correct course of action for the submarine. Because the internal representation of an image is simply a large matrix of numbers, the vision system's job can be thought of as filtering this large volume of mostly extraneous data to a few pieces of useful data, which the control system can then analyze.

\subsection{Vision Hardware}
The hardware for the vision subsystem consists of two cameras and a small netbook. Both cameras are Logitech Webcam 9000 Pro webcams, one of which points forward, and the other of which points down. These cameras were chosen for their price (about \$50 each) and the availability ofLinux driver support. While the cameras are not specifically designed for underwater or low light conditions, they have worked quite well in our pool testing. The netbook used is an HP Atom netbook. This model was chosen for its small size and low cost.

\subsection{Vision Software}
All of our image processing code is written in C++, using the OpenCV library. A large number of algorithms were tried and discarded during the development of our final flow.  Due to the scope of this document only the final algorithms used will be described.

The image processing flow can be broken up into three distinct parts: image segmentation (separating a 3-channel image into 1-channel pieces based primarily on color), object recognition (classification of each segment as background or target) and property calculation (deriving the object's properties such as location or color). The algorithm used for each step is distinct and will be discussed below.

Image segmentation is performed using OpenCV's implementation of the Watershed algorithm. The algorithm works iteratively from a collection of segmented pixels (seeds) and at each step associates the most similar pixel adjacent to a segmented pixel with that segment. It returns a grayscale image, with different gray levels corresponding to different segments. Each seed pixel has a value associated and two seeds of the same value will contribute to a single segment.

The performance of the Watershed algorithm is heavily dependent on the quality of the seeding. Optimally we want at least one seed for each different object in the image and at least one seed for the background. A single object should not have two different valued seeds, as this will cause two segments to emerge. To seed the algorithm, we take a random sample of pixels from the source image, and run K-Means clustering to cluster the samples based on color similarity. The results of the clustering is a minimum collection of pixels which are representative of the color space of the image. The clustering results used to assign values to the seeds - similarly colored seeds will get the same values (Figures~\ref{seed} and \ref{segment}).

\begin{figure}
\begin{center}
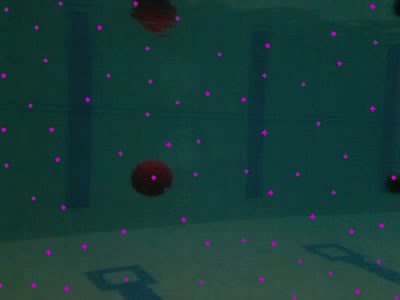
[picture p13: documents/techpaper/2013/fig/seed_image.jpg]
 
\caption{Example image at a test pool, with seed locations overlayed.}\label{seed}
\end{center}
\end{figure}

\begin{figure}
\begin{center}
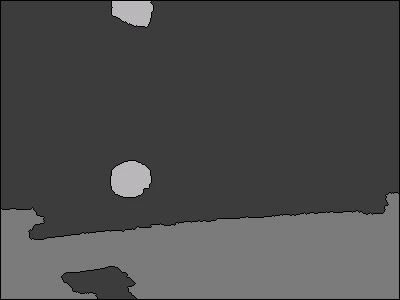
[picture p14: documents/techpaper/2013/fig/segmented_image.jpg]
 
\caption{The test image segmented.}\label{segment}
\end{center}
\end{figure}

Object recognition is made simple due to the fact that only circles and rectangles need to be recognized for the tasks we are aiming to do. OpenCV can find the minimum enclosing circle and (rotated) box for any segment, and a simple comparison of area, perimeter, and various symmetry properties can be performed to check if the segment is similar to its enclosing shape. For example, a the minimum enclosing circle of a non-circular segment will leave large amounts of blank space, and will therefore have a very different area compared to the segment.

Property calculation is done on a target-by-target basis. For most targets (the buoy, for example), it is  sufficient to know the position and characteristic dimension in pixel space. We can then use these numbers, along with the camera's field-of-view and the physical length to calculate the position and range of the object in real space. For the pipes at the bottom of the pool, the position angle is also needed. All of the pixle properties are easily extracted from the enclosing shape derived by OpenCV. To identify an object's color, we convert the BGR color of the object into HSV, which is more robust against changes in brightness, and use the resulting hue value to determine the color of the object.

Finally, in order for the vision code to return stable results and be robust against noise, we store the objects identified in the current frame begin processed as well as a number of frames prior. We use this to average and filter the numerical information from multiple frames. This allows us some room for error - a single frame with poor segmentation or a stray object will not destroy the system's performance.

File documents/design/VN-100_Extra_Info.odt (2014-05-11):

VN-100 Rugged

Useful Information not in manual

The following information was obtained from direct email correspondence between VectorNav and Alex Piggott during the month of August 2012.

CONNECTORS

Connector on the Rugged side: Harwin M80-05001042

Matching connector for the cable: Harwin M80-4861005

These connectors are usually available on Mouser.

QUATERNION CONVENTIONS

The IMU frame is a right-handed coordinate frame with the axes indicated on the VN-100 Rugged case. To map a vector from the world frame into the IMU frame, you would need to convert the quaternion vector into a direction cosine matrix and multiply that DCM into the world frame vector:

DCM(q)*v = V

where:

v = world-frame vector

V = IMU-frame vector

and DCM(q) is defined by:

Note: the above notation has the scalar component of the quaternion denoted by q0, the VectorNav units use q4 as the scalar component.

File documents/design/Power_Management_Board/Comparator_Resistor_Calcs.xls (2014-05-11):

Nominal | Measure | Ratio | Ra | Rb_ideal | Rb_real | Ratio_actual | Trigger_actual | Percent_Trigger
24 | 20 | 0.03 | 100000 | 3092.783505 | 3090 | 0.02997 | 20.02 | -0.1659385113
12 | 12.84 | 0.04672897196 | 100000 | 4901.960784 | 4870 | 0.04644 | 12.92 | 0.07669404517
12 | 11.16 | 0.05376344086 | 100000 | 5681.818182 | 5760 | 0.05446 | 11.02 | -0.08194444444
5 | 5.35 | 0.1121495327 | 100000 | 12631.57895 | 12700 | 0.11269 | 5.32 | 0.06488188976
5 | 4.65 | 0.1290322581 | 100000 | 14814.81481 | 14700 | 0.12816 | 4.68 | -0.06367346939
3.3 | 3.531 | 0.1699235344 | 100000 | 20470.82907 | 20500 | 0.17012 | 3.53 | 0.06873614191
3.3 | 3.069 | 0.1955034213 | 100000 | 24301.33657 | 24300 | 0.19549 | 3.07 | -0.06995884774
Notes:
1) Trigger voltages are +/- 7% of nominal voltages
2) Comparator has 0.6V references
3) Input bias current is 10nA => for <1% error due to input bias currents, require < 600kOhm resistance

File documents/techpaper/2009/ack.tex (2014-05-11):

\section{Acknowledgments}
\label{ack}
\vspace{-.03in}

We would like to thank the staff of the University of Toronto for
supporting our project, in particular: Barbara Ellenson, and Austra Ozolins.

We would also like to thank all our sponsors who have helped make this
project possible: The University of Toronto Engineering Alumni
Association, The Edward S. Rogers Department of Electrical and
Computer Engineering, The Division of Engineering Science, the
University of Toronto Engineering Society, Black and Decker and Digikey.

\commented {
, Romor Atlantic
Ltd, McQuest Marine, Sunstone Circuits, Xess, Sensor
Technology and SeaBotix.

\begin{figure}[h]
\begin{center}
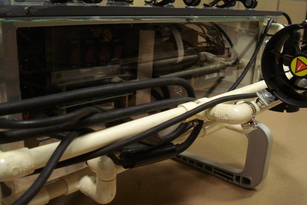
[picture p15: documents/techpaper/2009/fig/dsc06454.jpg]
  
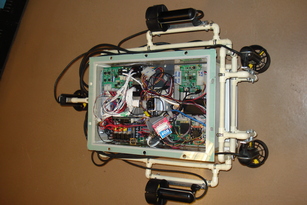
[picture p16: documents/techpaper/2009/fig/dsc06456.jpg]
  
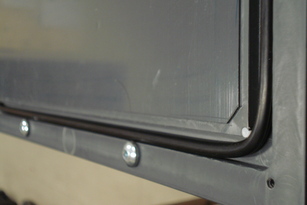
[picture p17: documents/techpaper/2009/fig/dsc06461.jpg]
  
\vspace{.05in}
\hrule
\caption{Other.}\label{oring}
\end{center}
\end{figure}
\begin{figure}[h]
\begin{center}
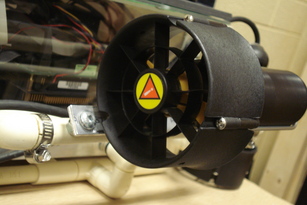
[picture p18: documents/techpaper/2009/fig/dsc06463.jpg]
  
\vspace{.05in}
\hrule
\caption{Other.}\label{oring}
\end{center}
\end{figure}
\begin{figure}[h]
\begin{center}
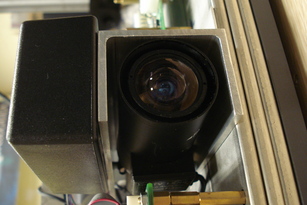
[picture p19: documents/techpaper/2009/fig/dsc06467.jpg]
  
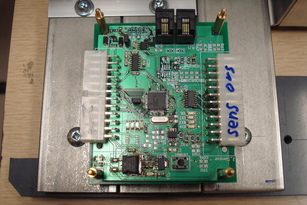
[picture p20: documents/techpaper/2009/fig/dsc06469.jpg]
  
\vspace{.05in}
\hrule
\caption{Other.}\label{oring}
\end{center}
\end{figure}
}

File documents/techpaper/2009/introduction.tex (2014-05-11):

\section{Introduction} 

The construction of the vehicle that our team will present at the
2009 Autonomous Underwater Vehicle (AUV) competition encompasses several new achievements. We explain the
context of our realization by first describing the main
objectives of the competition and how our team is organized.

\subsection{Overview of the Mission}

The objective of the competition is to build an autonomous underwater
vehicle to perform various tasks involving image recognition, and
passive sonar to
interact with its environment. For the vision tasks, the vehicle must 
pass through a validation gate, hit a buoy, follow a pipe, deposit an object
 in a box after passing under a set of horizontal pipes, resume following
 the pipe and launch a projectile through a rectangle target. The sonar tasks consists of
grabbing an object on top of an acoustic pinger and surface above it.
The details of the required tasks for the vehicle are described in the
 mission specification on the AUVSI website\footnote[1]{http://www.auvsi.org/competitions/water.cfm}.
 Through the design and testing phases, emphasis was placed on minimizing the weight 
 of the vehicle and the time required to complete the mission.

\subsection{The Team}
The team consists of twenty members that are divided into four subsystems: administration, frame, embedded electronics, and software. In order to maintain a high degree of integration throughout the project, members typically work in more than one subsystem. Our hardware is obtained through sponsorship and funding from our university (see Section~\ref{ack}). 

Figure~\ref{organi} illustrates the major components of the AUV
and the reader should refer to it often as we describe the innovative
aspects of those components in the following sections.

\begin{figure*}
\begin{center}
 
\caption{Organization of the AUV modules and their connectivity.}\label{organi}
\end{center}
\end{figure*}

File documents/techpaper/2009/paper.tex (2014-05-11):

\documentclass[12pt]{article}

%\usepackage{times}
%nips02e

\usepackage{spconf}
\usepackage{epsfig}
%\usepackage{psfig}
\usepackage{amsmath}
\usepackage[sort]{cite}
\usepackage{supertabular}
%\usepackage{dcolumn}
\usepackage{multirow}
\usepackage{rotating}
\usepackage{subfigure}
\usepackage{url}
\usepackage{bigstrut}
\usepackage{hhline}
%\usepackage{setspace}
\usepackage{slashbox}
\usepackage[T1]{fontenc} % for bold small caps

\tolerance=1000
\hyphenpenalty=2000

%\textwidth 6.5in
%\textheight 9.0in
%\headheight 0.0in
%\headsep 0.0in
%\oddsidemargin 0.0in
%\evensidemargin 0.5in
\renewcommand{\topmargin}{-.25in} % AAA
\newcommand{\commented}[1]{}

%\global\boilerplate={}
%\global\copyrightetc{}

\newenvironment{packed_enum}{
\begin{enumerate}
  \setlength{\itemsep}{1pt}
  \setlength{\parskip}{0pt}
  \setlength{\parsep}{0pt}
}{\end{enumerate}}

\title{  AquaTux }
\name{Josh Dian, Mark Harfouche, Lawrence Lee, Martin~Labrecque,
  Shervin Mehryar,\vspace{-.3in}}
\address{\em{Theodore Soong}$^+$\thanks{$^+$in alphabetical order} \\ University of Toronto Mechatronics Design Association\\
email: mech.design@utoronto.ca }

\usepackage{comment}
% Un-comment one of the following two lines to turn pdf links on/off
%\includecomment{pdfrefs}
\excludecomment{pdfrefs}

\begin{pdfrefs}
\usepackage[ps2pdf]{hyperref}
% (See the hyperref package documentation for a list of supported drivers.)
\hypersetup{
    pdftitle={  AquaTux },
    pdfauthor={Josh Dian, Mark Harfouche, Lawrence Lee, Martin Labrecque,
      Shervin Mehryar, Theodore Soong},
    pdfsubject={AUVSI 2009},
    pdfkeywords={Mechatronics Design Association, AUV, submarine}
}
\end{pdfrefs}

%for subfigure
\renewcommand{\subfigcapskip}{0mm}
\renewcommand{\subfigtopskip}{0mm}
\renewcommand{\subfigbottomskip}{2mm}

\renewcommand{\topfraction}{0.999}     % max fraction of floats at top
\renewcommand{\bottomfraction}{0.99}        % max fraction of floats at bottom
\renewcommand{\floatpagefraction}{0.99}

\usepackage{amssymb}
\usepackage{fancyhdr}

\lhead{}
\chead{}
\rhead{}
\lfoot{}
\cfoot{Mechatronics Design Association -- University of Toronto}
\rfoot{\thepage}
\renewcommand{\headsep}{10pt}   %AAAA
\renewcommand{\headrulewidth}{2pt}
\renewcommand{\footrulewidth}{2pt}

\pagestyle{fancy}
\hyphenation{program-mable}
\hyphenation{pipe-lined}
\hyphenation{Chem-que}

\makeatletter
\renewcommand\maketitle{%
 \begin{minipage}[h]{.3\textwidth} 
   \centering 
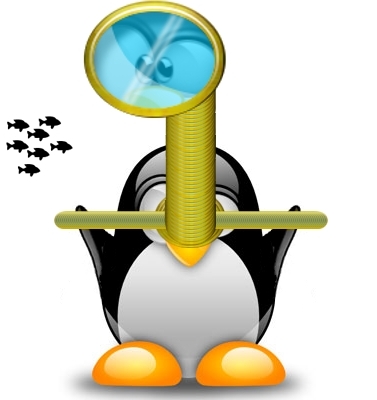
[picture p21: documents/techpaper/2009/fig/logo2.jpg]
    
 \end{minipage}% 
 \begin{minipage}[h]{.7\textwidth} 
   \centering 
\vspace{.3in}
\Huge{AquaTux} \\
\vspace{.1in}
\large{ Josh~Dian, Mark~Harfouche, Lawrence~Lee, Martin~Labrecque, Shervin~Mehryar, Theodore~Soong }\\
\normalsize{ University of Toronto Mechatronics Design Association\\
 email: mech.design@utoronto.ca }

 \end{minipage} 
\vspace{.3in}
\par}
\let\after@maketitle\@empty
\makeatother
\begin{document}

%%%%%%%%%%%%%%%%%%%%%%%%%%%%%%%%%%%%%%%%%%%%%%%%%%%%%%%%%%%%%%%%%%%%%%%%%%%%%%%%

\twocolumn[\maketitle]

\thispagestyle{fancy} 

\begin{abstract}
\input{abstract}
\end{abstract}

\vspace{-.1in}
\input{introduction.tex}
\vspace{-.1in}
\input{frame.tex}
\vspace{-.1in}
\input{electronics.tex}
\vspace{-.1in}
\input{sonar.tex}
\vspace{-.1in}
\input{vision.tex}
\vspace{-.12in}
\input{conclusions.tex}
\vspace{-.12in}
\input{ack.tex}
%\vspace{-.08in}
\small
%\bibliographystyle{IEEEtran}
%\bibliography{IEEEabrv,paper}

\end{document}

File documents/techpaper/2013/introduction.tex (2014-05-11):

\section{Introduction} 

The construction of the vehicle that our team will present at the
2013 Autonomous Underwater Vehicle (AUV) competition encompasses several new achievements. We explain the
context of our realization by first describing the main
objectives of the competition and how our team is organized.

\subsection{Overview of the Mission}

The objective of the competition is to build an autonomous underwater
vehicle to perform various tasks involving image recognition, and
passive sonar to
interact with its environment. For the vision-guided tasks, the vehicle must 
pass through a validation gate, hit buoys, follow pipes,
pass through set of pipes, drop an object
in a box, launch a projectile through a hexagonal target, and manipulating a wheel.
The sonar tasks consists of
grabbing an object on top of an acoustic pinger and surfacing above it.
The details of the required tasks for the vehicle are described in the
 mission specification on the AUVSI website\footnote[1]{http://www.auvsifoundation.org/foundation/competitions/robosub/}.
Through the design and testing phases, emphasis was placed on
performing a subset of these tasks well rather than attempting all tasks.

\subsection{The Team}
The team consists of twenty members that are divided into three subsystems: mechanical, electronics, and software. In order to maintain a high degree of integration throughout the project, members are encouraged to work in projects that span multiple subsystems. Our hardware is obtained through sponsorship and funding from our university (see Section~\ref{ack}). 

Figure~\ref{organi} illustrates the major components of the AUV
and the reader should refer to it often as we describe the innovative
aspects of those components in the following sections.

\begin{figure*}
\begin{center}
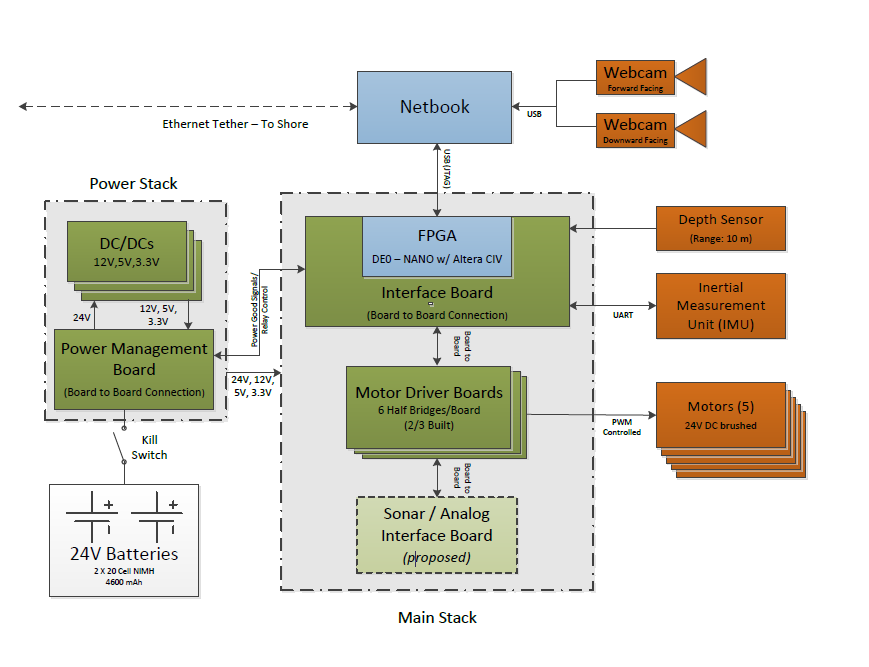
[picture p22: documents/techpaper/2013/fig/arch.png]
 
\caption{Organization of the AUV modules and their connectivity.}\label{organi}
\end{center}
\end{figure*}

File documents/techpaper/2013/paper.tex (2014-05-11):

\documentclass[12pt]{article}

%\usepackage{times}
%nips02e

\usepackage{spconf}
\usepackage{epsfig}
%\usepackage{psfig}
\usepackage{amsmath}
\usepackage[sort]{cite}
\usepackage{supertabular}
%\usepackage{dcolumn}
\usepackage{multirow}
\usepackage{rotating}
\usepackage{subfigure}
\usepackage{url}
\usepackage{bigstrut}
\usepackage{hhline}
%\usepackage{setspace}
%\usepackage{slashbox}
\usepackage[T1]{fontenc} % for bold small caps

\tolerance=1000
\hyphenpenalty=2000

%\textwidth 6.5in
%\textheight 9.0in
%\headheight 0.0in
%\headsep 0.0in
%\oddsidemargin 0.0in
%\evensidemargin 0.5in
\renewcommand{\topmargin}{-.25in} % AAA
\newcommand{\commented}[1]{}

%\global\boilerplate={}
%\global\copyrightetc{}

\newenvironment{packed_enum}{
\begin{enumerate}
  \setlength{\itemsep}{1pt}
  \setlength{\parskip}{0pt}
  \setlength{\parsep}{0pt}
}{\end{enumerate}}

\title{  AquaTux }
\name{David Biancolin, Adam Suban-Loewen, Victor Zhang, Ritchie Zhao}
\address{University of Toronto Mechatronics Design Association\\
email: mech.design@utoronto.ca }

\usepackage{comment}
% Un-comment one of the following two lines to turn pdf links on/off
%\includecomment{pdfrefs}
\excludecomment{pdfrefs}

\begin{pdfrefs}
\usepackage[ps2pdf]{hyperref}
% (See the hyperref package documentation for a list of supported drivers.)
\hypersetup{
    pdftitle={ AquaTux },
    pdfauthor={David Biancolin, Adam Suban-Loewen Victor Zhang, Ritchie Zhao},
    pdfsubject={AUVSI 2013},
    pdfkeywords={Mechatronics Design Association, AUV, submarine}
}
\end{pdfrefs}

%for subfigure
\renewcommand{\subfigcapskip}{0mm}
\renewcommand{\subfigtopskip}{0mm}
\renewcommand{\subfigbottomskip}{2mm}

\renewcommand{\topfraction}{0.999}     % max fraction of floats at top
\renewcommand{\bottomfraction}{0.99}        % max fraction of floats at bottom
\renewcommand{\floatpagefraction}{0.99}

\usepackage{amssymb}
\usepackage{fancyhdr}

\lhead{}
\chead{}
\rhead{}
\lfoot{}
\cfoot{Mechatronics Design Association -- University of Toronto}
\rfoot{\thepage}
\fancyheadoffset{0cm}
\renewcommand{\headsep}{10pt}   %AAAA
\renewcommand{\headrulewidth}{2pt}
\renewcommand{\footrulewidth}{2pt}
\renewcommand{\footskip}{0.5in}

\pagestyle{fancy}
\hyphenation{program-mable}
\hyphenation{pipe-lined}
\hyphenation{Chem-que}

\makeatletter
\renewcommand\maketitle{%
 \begin{minipage}[h]{.3\textwidth} 
   \centering 
    
 \end{minipage}% 
 \begin{minipage}[h]{.7\textwidth} 
   \centering 
\vspace{.3in}
\Huge{AquaTux} \\
\vspace{.1in}
\large{ David~Biancolin, Adam~Suban-Loewen, Victor~Zhang, Ritchie~Zhao }\\
\normalsize{ University of Toronto Mechatronics Design Association\\
 email: mech.design@utoronto.ca }

 \end{minipage} 
\vspace{.3in}
\par}
\let\after@maketitle\@empty
\makeatother
\begin{document}

%%%%%%%%%%%%%%%%%%%%%%%%%%%%%%%%%%%%%%%%%%%%%%%%%%%%%%%%%%%%%%%%%%%%%%%%%%%%%%%%

\twocolumn[\maketitle]

\thispagestyle{fancy} 

\begin{abstract}
\input{abstract}
\end{abstract}

\vspace{-.1in}
\input{introduction.tex}
\vspace{-.1in}
\input{frame.tex}
\vspace{-.1in}
\input{electronics.tex}
\vspace{-.1in}
\input{embedded.tex}
\vspace{-.1in}
\input{software.tex}
\vspace{-.1in}
\input{conclusions.tex}
\vspace{-.1in}
\input{ack.tex}
%\vspace{-.08in}
%\small
%\bibliographystyle{IEEEtran}
%\bibliography{IEEEabrv,paper}

\end{document}

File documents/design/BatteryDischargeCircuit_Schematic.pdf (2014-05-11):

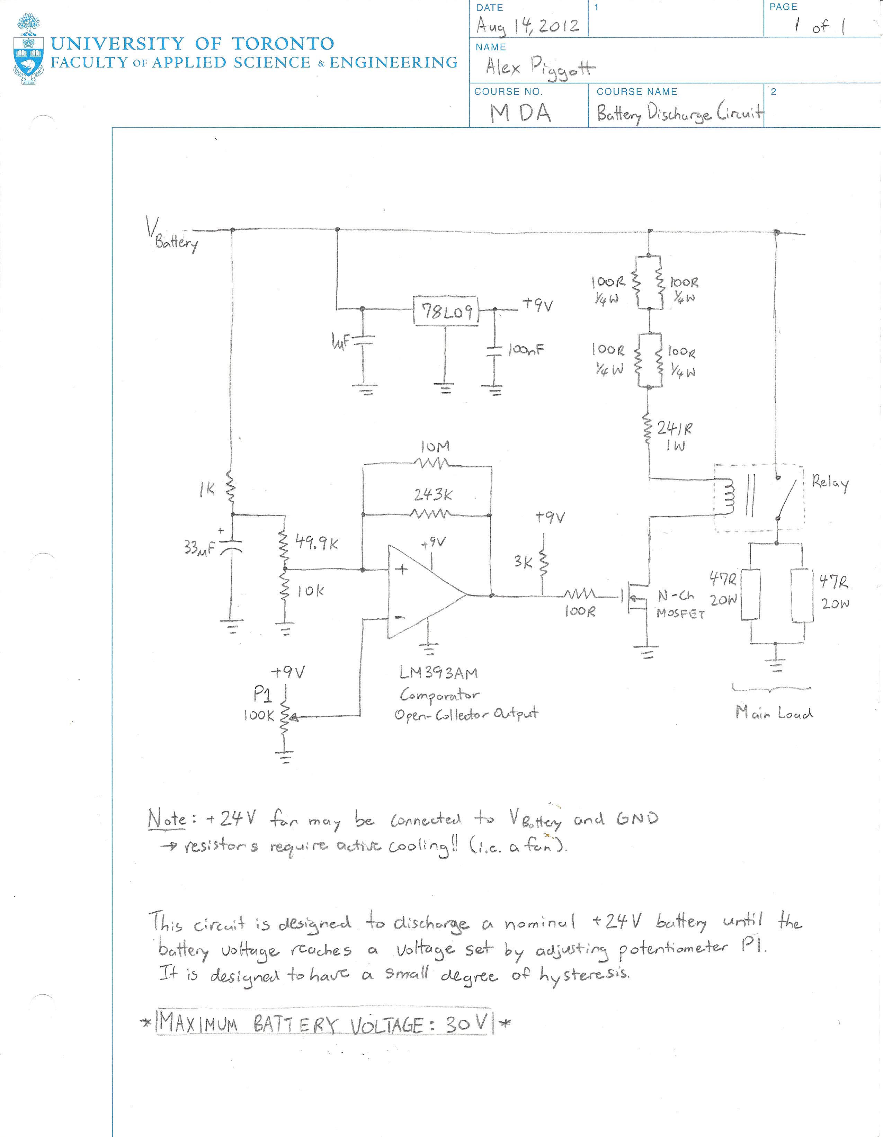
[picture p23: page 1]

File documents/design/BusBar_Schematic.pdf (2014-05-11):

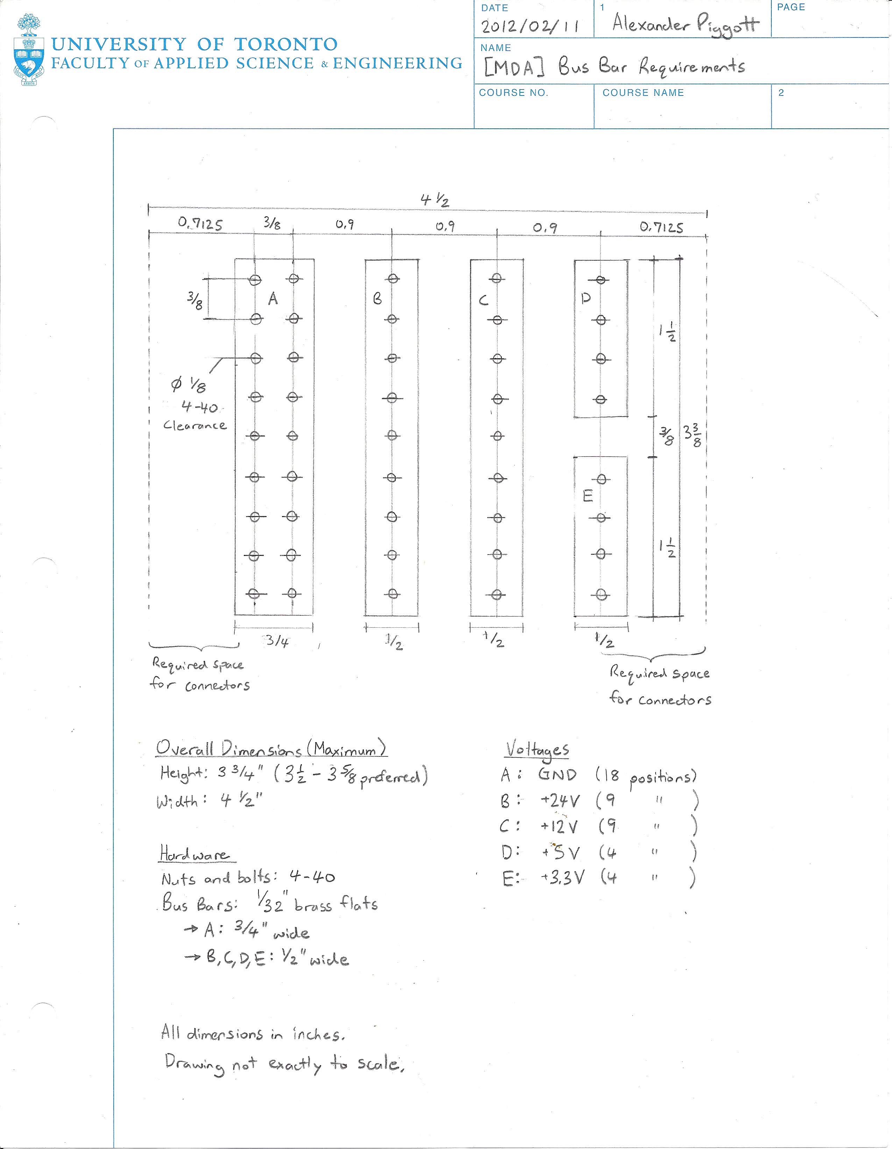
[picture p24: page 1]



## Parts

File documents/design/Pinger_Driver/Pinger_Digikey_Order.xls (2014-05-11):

Digikey PN | Manufacturer PN | Manufacturer | Description | Price | Quantity | Total Cost
285-1893-ND | LS35-24 | TDK-Lambda | 24V @ 1.5A AC-DC Power Supplies | 20.38 | 2 | 40.76
160-1358-5-ND | LTV-815 | LITE-ON | Optoisolator- 1Ch, Darlington Output, 4-DIP | 0.54 | 2 | 1.08
AE10022-ND | AR06-HZL-TT-R | Assmann WSW Components | 6-DIP socket | 0.48 | 2 | 0.96
2N7000TACT-ND | 2N7000TA | Fairchild Semiconductor | MOSFET N-Ch, 60V, 200mA, TO-92 | 0.44 | 2 | 0.88
CH770-ND | LRA32H2FBBNN | Cherry | Switch Rocker DPST 10A 125V | 1.46 | 1 | 1.46
A32340-ND | 5227726-2 | TE Connectivity | BNC Panel-mount jack | 3.50 | 1 | 3.50
A98505-ND | 1546306-4 | TE Connectivity | Barrier strip - 4 x 2 (double row) | 1.53 | 1 | 1.53
708-1329-ND | PF0001/63 | Bulgin | Power entry module with 6.3mm fuse | 3.57 | 1 | 3.57
F4186-ND | 01000058Z | Littelfuse Inc | Fuse clip (1/4") | 0.22 | 10 | 2.18
255-2098-5-ND | ALE14B24 | Panasonic Electric Works | Relay General Purposes SPST 16A 24V | 2.74 | 1 | 2.74
208697-2-ND | 208697-2 | TE Connectivity | Power Outlet Assembly | 1.49 | 1 | 1.49
HM1200-ND | 1550N | Hammond Manufacturing | Box Aluminum 9.85 x 9.85 x 3.99" Natural | 52.34 | 1 | 52.34
F1759-ND | 0312001.MXP | Littelfuse Inc | Fuse 1A 1" x 1 1/4", fast | 0.37 | 6 | 2.22
F1765-ND | 0313001.MXP | Littelfuse Inc | Fuse 1A 1" x 1 1/4", slow | 1.07 | 2 | 2.14
 |  |  |  |  | Shipping | 8.00
 |  |  |  |  | Subtotal | 124.85
 |  |  |  |  | Tax | 16.23
 |  |  |  |  | Total | 141.08

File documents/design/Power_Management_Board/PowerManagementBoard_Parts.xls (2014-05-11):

Description | Manufacturer | Digikey PN | Manufacturer PN | Package | Quantity
Relay (General Purpose), SPST, 30A 24V | Panasonic Electric Works | 255-2818-ND | JTV1AS-PA-24V | Through-Hole | 1
Magnetic Reed Switch | Cherry | CH405-ND | MP201801 |  | 1
Solid State Relay, 300mA, 1.15V input | Omron Electronics Inc-EMC Div | Z157-ND | G3VM-VF | Gull-wing SMD | 1
Comparator (push-pull, active-high, 0.6V ref) | Analog Devices Inc | ADCMP356YKSZ-REEL7CT-ND | ADCMP356YKSZ-REEL7 | SC-70-4 | 7
Multiplexer (8:1, 2-6V supply) | STMicroelectronics | 497-7348-1-ND | M74HC151TTR | 16-TSSOP | 1
N-Ch MOSFET (logic level) | Diodes/Zetex | ZXM61N02FCT-ND | ZXM61N02FTA | SOT-23-3 | 1
Schottky Diode (inductor flyback) | Fairchild Semiconductor | SS16FSDKR-ND | SS16 | DO-214AC, SMA | 3
1uH inductor (shielded SMT, 17A) | Wurth Electronics Inc | 732-2162-1-ND | 7443340100 | SMT | 3
220uF capacitor (35V electrolytic) | Panasonic - ECG | PCE4444CT-ND | EEE-FP1V221AP | SMT | 3
10uF Capacitor (35V, Y5V) | Taiyo Yuden | 587-1352-1-ND | GMK316F106ZL-T | 1206 | 6
1uF Capacitor | N/A - MDA already has stock |  |  | 1206 | 3
220R (Solid-State Relay diode resistor) | N/A - MDA already has stock |  |  |  | 1
1K (FPGA output pull-down resistor) | N/A - MDA already has stock |  |  |  | 1
Terminal Block, 2-pos, 200 mil spacing | TE Connectivity | A98342-ND | 282841-2 | Through hole | 2
Terminal Block, 3-pos, 200 mil spacing | TE Connectivity | A98343-ND | 282841-3 | Through hole | 1
Terminal Block, 5-pos, 200 mil spacing | TE Connectivity | A98082-ND | 282841-5 | Through hole | 1
Comparator Resistors (all 1% precision)
100K | Yageo | 311-100KHRCT-ND | RC0603FR-07100KL | 0603 | 7
3.09k | Yageo | 311-3.09KHRCT-ND | RC0603FR-073K09L | 0603 | 1
4.87K | Yageo | 311-4.87KHRCT-ND | RC0603FR-074K87L | 0603 | 1
5.76K | Yageo | 311-5.76KHRCT-ND | RC0603FR-075K76L | 0603 | 1
12.7K | Yageo | 311-12.7KHRCT-ND | RC0603FR-0712K7L | 0603 | 1
14.7K | Yageo | 311-14.7KHRCT-ND | RC0603FR-0714K7L | 0603 | 1
20.5K | Yageo | 311-20.5KHRCT-ND | RC0603FR-0720K5L | 0603 | 1
24.3K | Panasonic - ECG | P24.3KHCT-ND | ERJ-3EKF2432V | 0603 | 1
Aside (replacement inductor if filtering doesn't work) => DO NOT ORDER THIS PART!
3.3uH inductor (shielded SMT, 14A) | Wurth Electronics Inc | 732-2165-1-ND | 7443340330 | SMT

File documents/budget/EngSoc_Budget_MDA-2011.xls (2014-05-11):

 |  |  | University of Toronto
 |  |  | Engineering Society
 |  |  | Club Budget
 |  |  | Send budgets to Jonathan Ng, Vice-President Finance
 |  |  | at vpfinance@skule.ca or submit to the EngSoc Office (SF B740)
 |  |  | Please accompany this budget with all relevant documents
 |  |  | (including price quotes, further commentaries, and other justifications)
 | Name: | Ritchie Zhao
 | Position: | Treasurer
 | Account/Committee: | Mechatronics Design Association
 | Proposed Net Expenses: | $6047.00 | Date: | 2019-07-01
 | Last Year's Net Expenses: | $1000.00
 | Description of Request/Notes:
 | Revenues
4600 | Expected revenue (selling tickets, fundraisers, etc) and short explanation |  |  | Amount Requested | Amount Approved | Spent to Date | Last Year
1 | Donation request to Altera |  |  | $237 in FPGAs | $237 in FPGAs | Item was donated | N.A.
2 | Funding Request to Division of Engsci |  |  | $1000.00 | $0.00 | $0.00 | $1125.00
3 | Funding Request to Department of ECE |  |  | $1000.00 | $0.00 | $0.00 | $1000.00
4 | Funding Request to Department of MIE |  |  | $1000.00 | $0.00 | $0.00 | $1000.00
5 | U of T Alumini |  |  | $1600.00 | $0.00 | $0.00 | $1600.00
6
7
8
9
10
11
12
13
14
15
16
 |  | Total Expected Revenue |  | $4600.00 | $0.00 | $0.00 | $4725.00
 | Expenses
1637 | Expected expenses (ie supplies, food, etc) and short explanation |  |  | Amount Requested | Amount Approved | Spent to Date | Last Year
1 | Pressure Gauge (air column pressure sensor) |  |  | $100.00
2 | Torpedo Launch Mechanism (compressed air/CO2 mechanism) |  |  | $200.00
3 | Vacuum Pump (to test hull integrity outside of water) |  |  | $350.00 |  |  |  | http://www.labwrench.com/
4 | Object Dropper (mechanism built. Need drivers) |  |  | $50.00 |  |  |  | Just need the driver board
5 | Manipulator Arm (arm to grab an object) |  |  | $200.00
6
7 | Onboard Computer (small cheap used netbook) |  |  | $500.00 |  |  |  | Find on Ebay/Craigslist
8 | Altera FPGAs (DE0 boards) |  |  | $237.00 | $237.00 | $237.00 | $0.00 | Donated by altera
9 | Wires and Connectors () |  |  | $100.00 |  |  | $400.00 | Last years were rubber waterproof ones
10 | Machine Vision Cameras |  |  | $100.00 |  |  |  | 2 of Logitech webcam c905, quickcam pro, or webcam pro9000, used. http://www.amazon.com/gp/offer-listing/B000RZQZM0?s=electronics&condition=used
11 | Hydrophone Boards |  |  | $250.00 |  |  |  | http://www.quickfiltertech.com/html/content_page.php?content_id=8&
12 | Depth Sensor |  |  | $100.00
13 | Inertial Measurement Unit (gyroscopes and accelerometers package) |  |  | $300.00 |  |  |  | http://www.pnicorp.com/products/prime
14 | Motor Controllers |  |  | $700.00 |  |  |  | We have detail calculations for this
15 | Battery Chargers |  |  | $100.00
16
17 | Pool Test Time |  |  | $750.00 |  |  |  | In previous years athletic center offered $75 per hour.
18 | Obstacle Course Materials (PVC piping of different colors, plexiglass boards, bouys, paint) |  |  | $100.00
19 | Contest Fee |  |  | $500.00 |  |  |  | http://www.auvsifoundation.org/AUVSI/FOUNDATION/Competitions/RoboSub/RoboSubOverview/Default.aspx
20 | Vehicle Shipment |  |  | $450.00 |  |  |  | To san diego and back. The vehicle is about 50cm x 40cm x 25cm and at least 30 kg.
21 | Van Rental for Transport (6 to 7 days) |  |  | $600.00 |  |  |  | budget, thrifty, etc. Need an SUV. Includes gas.
22
23 | Hull Mechanical Parts |  |  | $0.00 | $0.00 | $0.00 | $200.00
24 | Sonar DSP Board |  |  | $0.00 | $0.00 | $0.00 | $200.00
25 | Active Electronic Components (microcontrollers, chips) |  |  | $0.00 | $0.00 | $0.00 | $200.00
26 | Recruitment events and social outings |  |  | $300.00 |  |  |  | $100 for pizza at the recruitment event, $200 for a bar social
27
28 | Contingency (please budget 5% on unknown costs) |  |  | $0.00 | $0.00 | $0.00 | $0.00 | Our cost estimates already have a margin of error, this seems unecessary
 | Subtotal |  |  | $5987.00 | $237.00 | $237.00 | $1000.00
 | HST (13%) |  |  | $0.00 | $0.00 | $0.00 | $0.00 | Again, this is mostly accounted for.
 |  | Total Expected Expenses |  | $5987.00 | $237.00 | $237.00 | $1000.00
 | Reserved for Finance Committee
 | Outcome: | o Approved |  | o Returned
 | Recommended Funding:
 | Notes:

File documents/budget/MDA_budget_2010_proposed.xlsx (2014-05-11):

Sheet: Sheet1
 | Expected Expenses | Unit cost | Units | Total | Envisionned Sponsor
Mechanical | Pelican Case for new Hull | $75.00 | 1 | $75.00 | UofT Department of Mechanical and Industrial Engineering
 | Vehicle material - Polycarbonate, PVC, aluminum | $300.00 | 1 | $300.00
 | Mechanical Grabber | $250.00 | 1 | $250.00
 | Fabrication Cost | $400.00 | 1 | $400.00
 | Torpedo ammo, plastic prototyped | $100.00 | 4 | $400.00 | Proto3000
 | Fabrication tools | $300.00 | 1 | $300.00 | Black & Decker
 | Torpedo actuation Mechanism | $150.00 | 2 | $300.00 | UofT Rogers Department of Electrical and Computer Engineering
Electrical | Passive electronic devices (resistors, capacitors, diodes, switches, relays) | $100.00 | 1 | $100.00 | 15% off from Digikey, UofT Rogers Department of Electrical and Computer Engineering
 | Active devices - micro controllers, amplifiers, voltage regulators, MOSFETs | $500.00 | 1 | $500.00
 | Wires and connectors | $100.00 | 1 | $100.00
 | Waterproof connectors | $100.00 | 4 | $400.00 | Teledyne Impulse Ent.
 | Digital multimeter | $150.00 | 2 | $300.00 | Fluke Corporation
 | Digital osciloscope | $950.00 | 1 | $950.00 | LeCroy
 | Printed Circuit Boards | $400.00 | 1 | $400.00 | Coretec Inc.
 | On-board netbook | $600.00 | 1 | $600.00 | Lenovo
Testing | Devellopment computer | $500.00 | 1 | $500.00
 | Pool time | $75.00 | 15 | $1125.00 | UofT Division of Engineering Science
 | PVC | $200.00 | 1 | $200.00 | University of Toronto Engineering Society
Competition costs | Contest entrance fee | $500.00 | 1 | $500.00
 | Shipment of tools and vehicle to and from San Diego | $1000.00 | 1 | $1000.00 | UofT Engineering Alumni
 | Ten day van rental in San Diego for transporting the vehicle to and from the hotel to the competition | $600.00 | 1 | $600.00
 |  |  | Total | $9300.00

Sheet: Sheet2
Subsystem | Description | Paid in 2008-2009 | Funding 2008-2009 | Expected Expense 2010-2011 | Funding Source 2010 - 2011
Mechanical | Pellican case for new hull | N/A | New addition in 2010/2011 | $75 | UofT Department of Mechanical and Industrial Engineering
 | PVC for frame | $200 | Office of the Provost | $150 | UofT Department of Mechanical and Industrial Engineering
 | Plastic for the hull | $100 | Office of the Provost | N/A | The new null is to use the pellican case
 | Aluminium for hull | $50 | Office of the Provost | $150 | UofT Department of Mechanical and Industrial Engineering
 | Mechanical Grabber | N/A | New addition in 2010/2011 | $250 | UofT Department of Mechanical and Industrial Engineering
 | Fabrication Costs | $300 | Retained Funds | $400 | UofT Department of Mechanical and Industrial Engineering
 | Torpedo ammo | N/A | New addition in 2010/2011 | $400 | Proto3000
 | Fabrication Tools | $400 | Black and Decker | $300 | Black and Decker
 | Torpedo actuation mechanism | N/A | New addition in 2010/2011 | $300 | Department of Electrical and Computer Engineering
Electrical | Passive electronic devices (resistors, capacitors, diodes, switches, relays) | $100 | 15% off Digikey, Department of Electrical and Computer Engineering | $100 | 15% off Digikey, Department of Electrical and Computer Engineering
 | Active devices - micro controllers, amplifiers, voltage regulators, MOSFETs | $600 | 15% off Digikey, Department of Electrical and Computer Engineering | $500 | 15% off Digikey, Department of Electrical and Computer Engineering
 | Wires | $50 | 15% off Digikey, Department of Electrical and Computer Engineering | $50 | 15% off Digikey, Department of Electrical and Computer Engineering
 | Connectors | $40 | 15% off Digikey, Department of Electrical and Computer Engineering | $50 | 15% off Digikey, Department of Electrical and Computer Engineering
 | Waterproof connectors | N/A | Needed for new actiontion mechanisms in 2010/2011 | $400 | Teledyne Impulse Ent.
 | Digital Multimeters | N/A | Borrowed from club members | $300 | Fluke Corporation
 | Variable voltage power supplies | $300 | Donation from the UofT ECE labs | N/A | Using old power supplies
 | Printed circuit boards | $400 | Deparetment of Electrical and Computer Engineering | $400 | Coretec Inc.
 | On board computer | N/A | The old computer was still functional | $600 | Lenovo Inc.
 | Digital Osciloscope | N/A | Using a previously donated analog osciloscope | $950 | LeCroy
Testing | Devellopment Computers | N/A | Using old computers | $500 | Lenovo Inc.
 | Pool time | N/A | Used the condo pool of a club member, this year, it was decided that the depth of this pool is no longer sufficient for our testing purposes | $1125 | UofT Division of Engineering Science
 | PVC | N/A | We did not build testing equipment this year | $200 | UofT Engineering Society
Competition Cost | Contest entrance fee | $500 | Alumni funding | $500 | UofT Engineering Society
 | Shipping | $800 | Division of Engineering Science + Alumni funding | $1000 | Alumni
 | Ten day van rental | N/A | A club member had a PEY job near San Diego and donated his car and gas for the competition | $600 | Alumni
 | Total | $3840 |  | $9300
Notes
 | Club activity was suspended during the year of 2009-2010 due to the fact that most club veterans were involved in other activities, Figures from 2008-2009 are shown instead.
 | Note increase in budget comes from envisionned corporate sponsors that would mainly donate testing and debugging equipment. The increase in members interested in contacting external companies has allowed us to be hopeful in obtaining the donated items. We have also had a great increase in members from the Department of Mechanical and Industrial Engineering which has allowed us to ask the Department for funding. Due to the increase in members interested in contacting sponsors, we are also requesting funding from the Engineering Society, a source that was not approached in the past.

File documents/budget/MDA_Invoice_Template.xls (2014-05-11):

 |  | INVOICE
Mechatronics Design Association
Engineering Society - University of Toronto
 |  | DATE:
10 King's College Road Suite B740 |  | 2011-07-27
Toronto, Ontario M5S 3G4
Phone 123-456-7890 |  | INVOICE #
 |  | 2011-001
Bill To: | For:
Mechatronics Design Association | KBC Tools Equipment
DESCRIPTION |  | AMOUNT
Mechanical tools and equipment bought from KBC, see attached sales reciept |  | $209.36
Same as above |  | 86.87
 | SUBTOTAL | $296.23
 | TAX RATE
 | TOTAL | $296.23
Make all checks payable to Mechatronics Design Association
If you have any questions concerning this invoice, contact:
Ritchie Zhao (Treasurer) at 416-272-8076 or ritchie.zhao@utoronto.ca

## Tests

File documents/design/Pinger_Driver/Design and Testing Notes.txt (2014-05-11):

%%%%%%%%%%%%%%%%%%%%%%%%%%%%%%%%%%%%%%%%%%%%%%%%
%                December, 2012                %
%%%%%%%%%%%%%%%%%%%%%%%%%%%%%%%%%%%%%%%%%%%%%%%%
Transformer winding calculations.
0) Design Parameters
Frequency: 12-30kHz
Power Dissipated: < 1W
Primary Voltage:   40Vpp
Secondary Voltage: 240Vpp (6 x turns ratio)

1) Magnetic losses
B = |V| / A w N
  where A = cross-sectional area
	N = number of turns
	w = angular frequency
	V = voltage amplitude (NOT rms)
	B = peak magnetic field (T)

For the ETD59 core used in the transformer (3F3 ferrite),
	A = 368 mm^2
	V = 51500 mm^3

	P = V * 10kW/m^3 @ 100mT, 25kHz (3F3 material)
	  = 0.515W (significant)
Thus, we plan to design the transformer with a max 50mT B-field.

Considering the primary (fewer turns), we have:
	|V| = 20V
	B   = 0.05T
	A   = 363mm^2
	w   = 2*pi*12e3;
	N   = (20)/(362e-6)(2*pi*12e3)(0.05) = 14.5 turns minimum

2) Shunt inductance
Inductance of core is given by:
L = N^2 A_L
  where A_L = 5.6 uH for the ETD59 core

If we try N = 31, we get:
	L = 25^2 (5.6uH) = 5380uH
At 12kHz, this has an impedance of 405 ohms, which is acceptably high.

3) Resistance calculations
	24AWG wire: 25.3 ohms/1000ft
	32AWG wire: 159.7 ohms/1000ft
Using a 25mm bobbin, we have ~80mm = 0.262 ft/turn.
Using N_primary = 31, N_secondary = 186:
	L_primary   = 6.55 ft
	L_secondary = 39.3 ft
With 24AWG wire (32AWG is unecessarily lossy):
	R_primary   = 0.166 ohms
	R_secondary = 0.994 ohms
Since the primary has 6x the current of the secondary, the primary is currently ~6x lossier than the secondary.
Thus, it is probably a good idea to use multiple strans for the primary.

Using 4 x 24AWG wire for the primary, 1x 24AWG for the secondary:
	R_primary   = 0.041 ohms
	R_secondary = 0.994 ohms

4) Turns per layer of bobbin
24AWG ~ 3/5mm = 0.6mm
Thus, with our 4cm bobbin => 66 turns / layer maximum (60 is easily achievable).

FINAL DESIGN:
-------------
Turns Ratio     - 1:6
Primary Turns   - 31
Secondary Turns - 186
Wire            - 24AWG (1x for secondary, 4x for primary)

%%%%%%%%%%%%%%%%%%%%%%%%%%%%%%%%%%%%%%%%%%%%%%%%
%                January, 2012                 %
%%%%%%%%%%%%%%%%%%%%%%%%%%%%%%%%%%%%%%%%%%%%%%%%
Transformer winding details
- secondary: 186 total (placed on INSIDE of winding)
	=> 1 x 24AWG
	=> layer 1 - 67
	     "   2 - 59
	     "   3 - 60
- primary: 31 total (placed on OUTSIDE of winding)
	=> 4 x 24AWG (to reduce winding resistance)
	=> layer 1 - 16
	     "   2 - 15
- used fish paper between all layers, and fully impregnated with red insulating varnish, to fully insulate the windings

%%%%%%%%%%%%%%%%%%%%%%%%%%%%%%%%%%%%%%%%%%%%%%%%
%           April 14, 2012 (Saturday)          %
%%%%%%%%%%%%%%%%%%%%%%%%%%%%%%%%%%%%%%%%%%%%%%%%
- tested and characterized transformer: quite impressive performance (measured characteristics using sine-wave generator, resistor, & scope)
	=> 6:1 ratio (+/- 0.3%) from 10-40kHz
	=> primary (fewer turns) leakage inductance: 6.14uH (10kHz) - 5.13uH (40kHz)
	=> primary (fewer turns) shunt impedance: 432 ohms (10kHz) - 4657 ohms (40kHz)
		- antiresonance @ 36kHz (shunt impedance goes to ~10,000 ohms)
		- inductive below 36kHZ, capacitive above 36kHz
	=> impedances of secondary are same as primary, except *approximately* converted via the impedance ratio (36 times larger)
- tested amplifier with transformer (open load), and 2 x 1uF capacitors in series with the primary coil
	=> no oscillations or other issues with amplifier
	=> successfully measured ~230Vpp at output of transformer using oscilloscope
	=> no distortions in transformer output signal

*** IMPORTANT ***: oscillator in pinger driver (oscillator) does NOT start unless the POSITIVE supply rail is turned on FIRST.

%%%%%%%%%%%%%%%%%%%%%%%%%%%%%%%%%%%%%%%%%%%%%%%%
%            April 24, 2012 (Tuesday)          %
%%%%%%%%%%%%%%%%%%%%%%%%%%%%%%%%%%%%%%%%%%%%%%%%
- characterized the impedance of the ultrasound transducer (Sensor Technology Limited SQ09 Transmit/Recieve hydrophone) using a sine-wave generator, resistor, and scope
	=> impedance modelled well by a 10nF capacitor over most of 10kHz - 40kHz range
	=> encounter some sort of acoustic resonance @ 30-33kHz: the impedance briefly transitions from capacitive to resistive, and the impedance becomes very sensitive to the presence of water (the addition of water can increase the impedance by a factor of two)
	=> over the rest of the range, the transducer is fairly insensitive to the presence of water; the impedance changes by less than 20%
		- tested pinger driver with ultrasound transducer: success!
	=> used total system: sine-wave generator, power amplifier, and transformer
	=> great performance: no stability issues, ringing, etc.
	=> over most of frequency range (12kHz - 32kHz), able to use max amplitude setting (~240Vpp)
	=> from ~28-31kHz (corresponding to resonance of transducer):
		- too much current drawn from power supplies used, which went into current-limiting mode
		- no distortion / current limiting if output is reduced to ~170-180Vpp
	=> system should work over entire range at 240Vpp if we use batteries

%%%%%%%%%%%%%%%%%%%%%%%%%%%%%%%%%%%%%%%%%%%%%%%%
%            April 24, 2012 (Tuesday)          %
%%%%%%%%%%%%%%%%%%%%%%%%%%%%%%%%%%%%%%%%%%%%%%%%
- fully tested the pinger driver with the ultrasound transducer: everything works well
- minor issue: when using external trigger, there is ~50mS delay until the output signal turns off (design error)
- measured frequency vs. frequency knob setting:

Setting		Frequency(kHz)
--------------------------------
0		12.0
10		13.5
20		15.9
30		18.0
40		20.2
50		22.5
60		25.0
70		27.3
80		29.6
90		31.7
100		32.6

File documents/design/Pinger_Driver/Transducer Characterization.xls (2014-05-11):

Frequency (KHz) | V_total (Vpp) | V_resistor (Vpp) | Z (assume reactive) | Z (assume resistive) | Z_ideal (10nF capacitor)
11.06 | 4.20 | 0.54 | 1542.6 | 1355.6 | 1439.0 | Capacitive
12.74 | 4.24 | 0.62 | 1353.0 | 1167.7 | 1249.3 | Capacitive
14.08 | 4.20 | 0.70 | 1183.2 | 1000.0 | 1130.4 | Capacitive
16.90 | 4.16 | 0.84 | 970.1 | 790.5 | 941.7 | Capacitive
19.03 | 4.16 | 0.94 | 862.2 | 685.1 | 836.3 | Capacitive
21.79 | 4.12 | 1.08 | 736.3 | 563.0 | 730.4 | Capacitive
24.50 | 4.08 | 1.22 | 638.3 | 468.9 | 649.6 | Capacitive
27.00 | 4.08 | 1.42 | 538.7 | 374.6 | 589.5 | Capacitive
29.20 | 3.96 | 1.60 | 452.8 | 295.0 | 545.1 | Capacitive
30.30 | 3.72 | 1.70 | 389.3 | 237.6 | 525.3 | Capacitive / Resistive
30.74 | 3.64 | 1.28 | 532.4 | 368.8 | 517.7 | Capacitive / Resistive
31.50 | 3.76 | 0.90 | 811.3 | 635.6 | 505.3 | Capacitive / Resistive
33.10 | 3.76 | 1.20 | 593.9 | 426.7 | 480.8 | Capacitive / Resistive
34.40 | 3.76 | 1.16 | 616.7 | 448.3 | 462.7 | Capacitive
36.13 | 3.76 | 1.32 | 533.4 | 369.7 | 440.5 | Capacitive
38.00 | 3.76 | 1.40 | 498.5 | 337.1 | 418.8 | Capacitive
40.40 | 3.68 | 1.56 | 427.3 | 271.8 | 393.9 | Capacitive
Measurement Details
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

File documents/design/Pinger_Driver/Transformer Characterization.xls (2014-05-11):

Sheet: Transformer Output Ratio
Frequency (kHz) | Primary (Vpp) | Secondary (Vpp) | Voltage Ratio
12.2 | 3.22 | 19.4 | 6.02
14.0 | 3.22 | 19.4 | 6.02
16.8 | 3.24 | 19.6 | 6.05
19.9 | 3.24 | 19.4 | 5.99
22.2 | 3.24 | 19.4 | 5.99
24.6 | 3.24 | 19.4 | 5.99
27.0 | 3.24 | 19.6 | 6.05
29.5 | 3.26 | 19.6 | 6.01
32.0 | 3.26 | 19.6 | 6.01
34.5 | 3.26 | 19.6 | 6.01
37.5 | 3.28 | 19.6 | 5.98
40.2 | 3.28 | 19.6 | 5.98
 |  | Average | 6.01
Measured with an OPEN load
Frequency response of transformer is almost perfectly flat.
Design voltage ratio is exactly 6.00; measured voltage is exactly as predicted

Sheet: Primary Imped - Open Secondary
Frequency (kHz) | V_total (Vpp) | V_resistor (mVpp) | Z_primary (ohms)
11.7 | 3.42 | 158 | 432.4491573
14.6 | 3.44 | 120 | 572.9843899
18.4 | 3.44 | 86 | 799.7499609
21.7 | 3.43 | 62.6 | 1095.664123
23.78 | 3.42 | 51.0 | 1341.027339
26.74 | 3.5 | 38.8 | 1804.012851
30.49 | 3.5 | 23.0 | 3043.412546
33.1 | 3.48 | 13.9 | 5007.154302
37.3 | 3.32 | 6.4 | 10374.98072
39.3 | 3.32 | 8.8 | 7545.428039
41.7 | 3.4 | 14.6 | 4657.491305
Placed 20ohm resistor in series with primary (fewer turns), OPEN secondary
Measured voltage across:
 | 1) Resistor
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

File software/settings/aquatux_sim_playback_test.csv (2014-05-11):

# Test video input
IMAGE_INPUT VIDEO
VIDEO_FWD sim.avi
VIDEO_DWN sim_dwn.avi
IMAGE_SHOW_RAW 1
WRITE_TO_VIDEO 0
ATTITUDE_INPUT NULL
OPERATION MANUAL
ACTUATOR_OUTPUT NULL

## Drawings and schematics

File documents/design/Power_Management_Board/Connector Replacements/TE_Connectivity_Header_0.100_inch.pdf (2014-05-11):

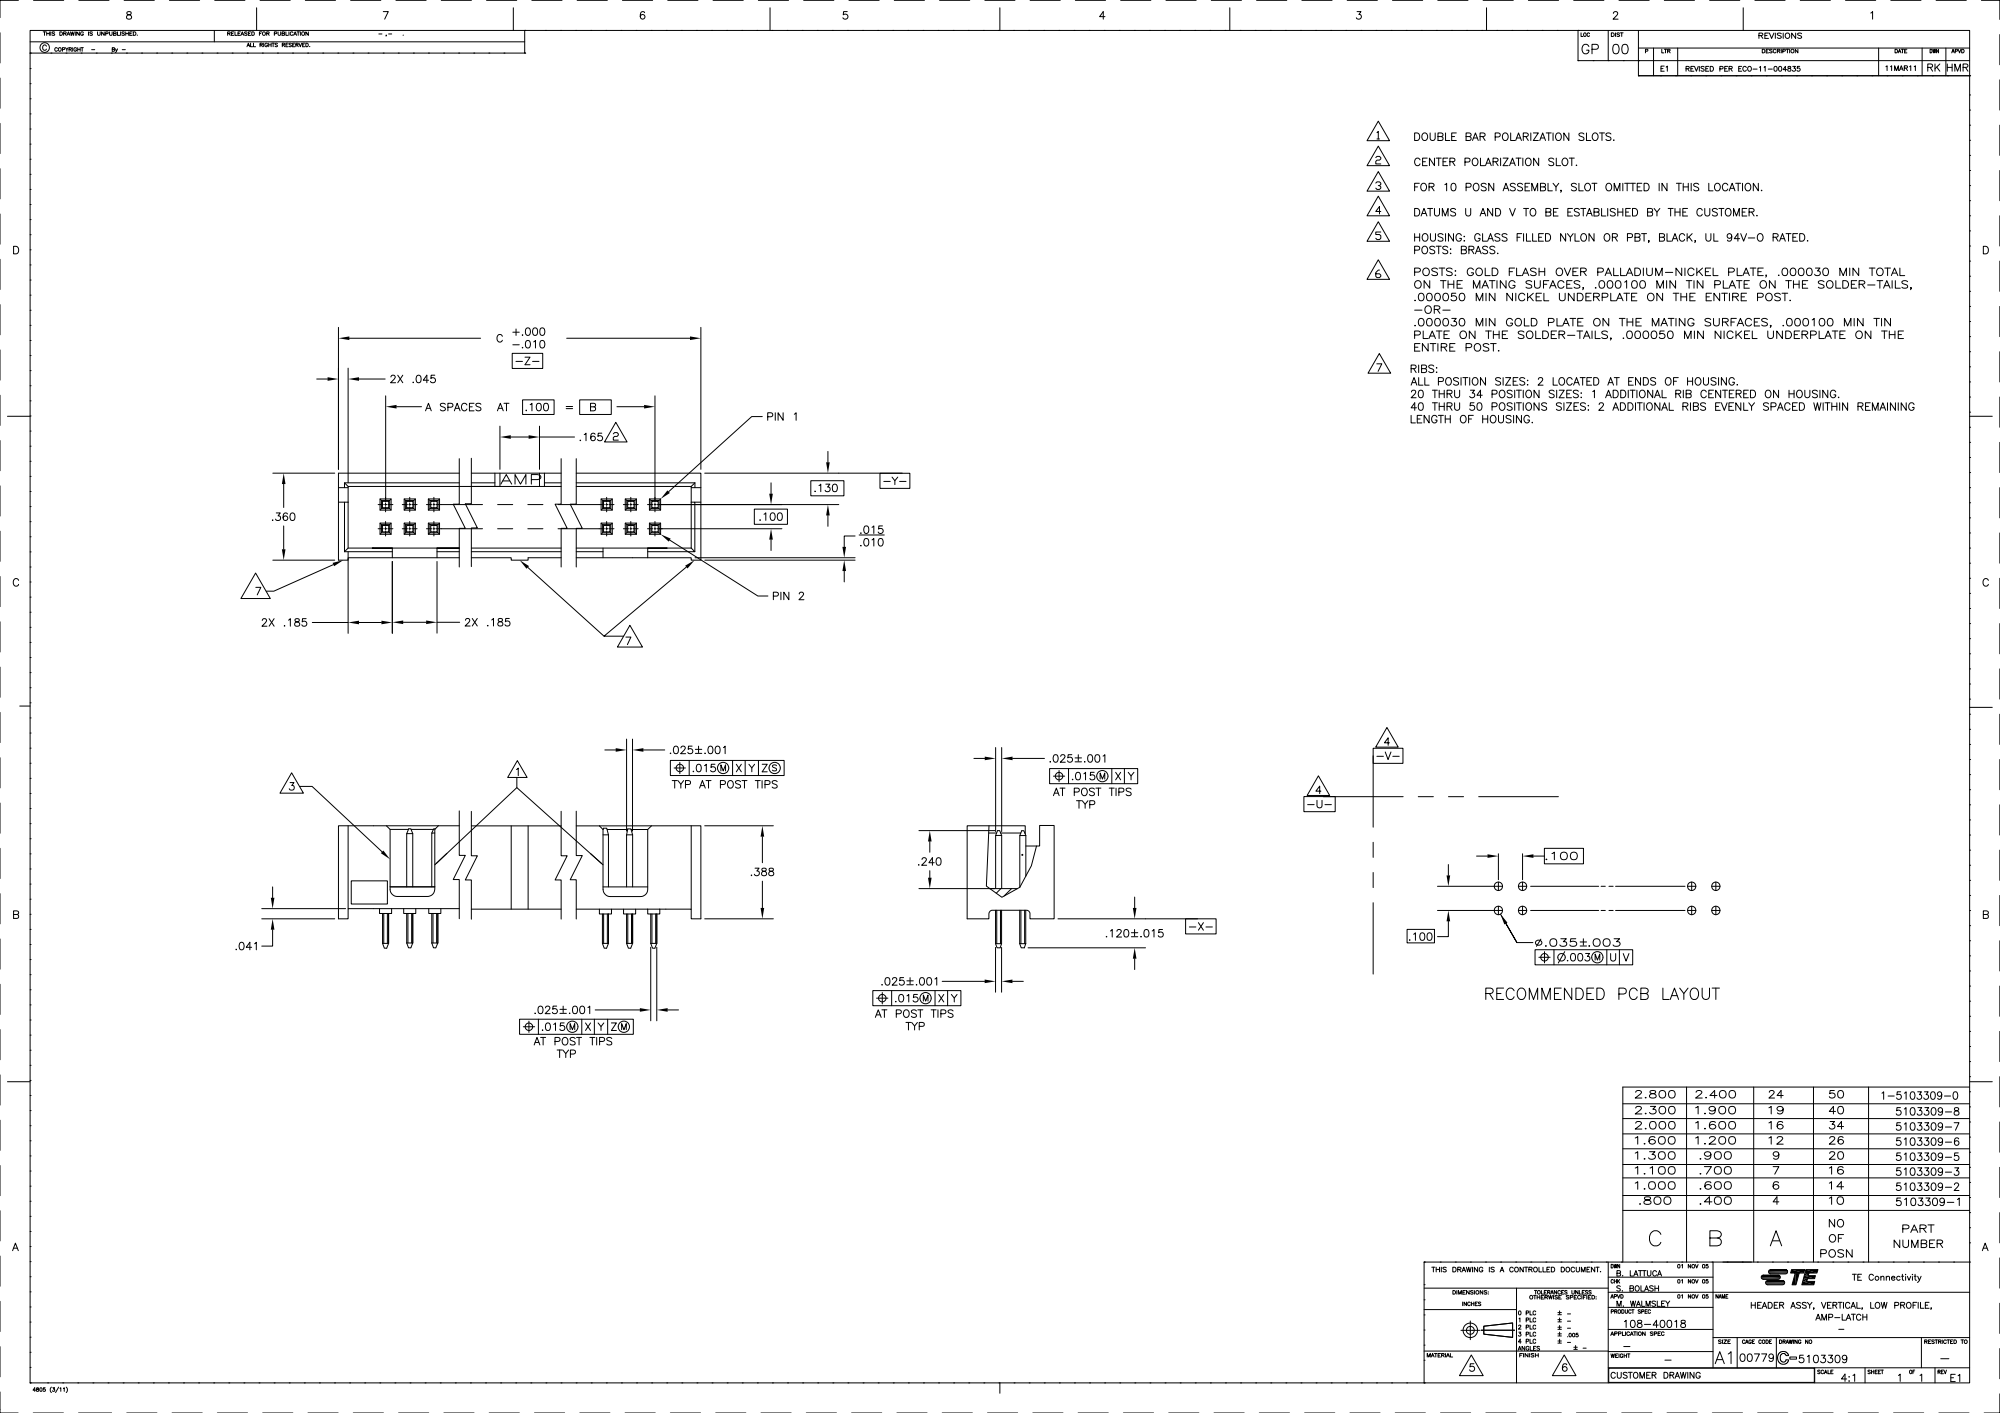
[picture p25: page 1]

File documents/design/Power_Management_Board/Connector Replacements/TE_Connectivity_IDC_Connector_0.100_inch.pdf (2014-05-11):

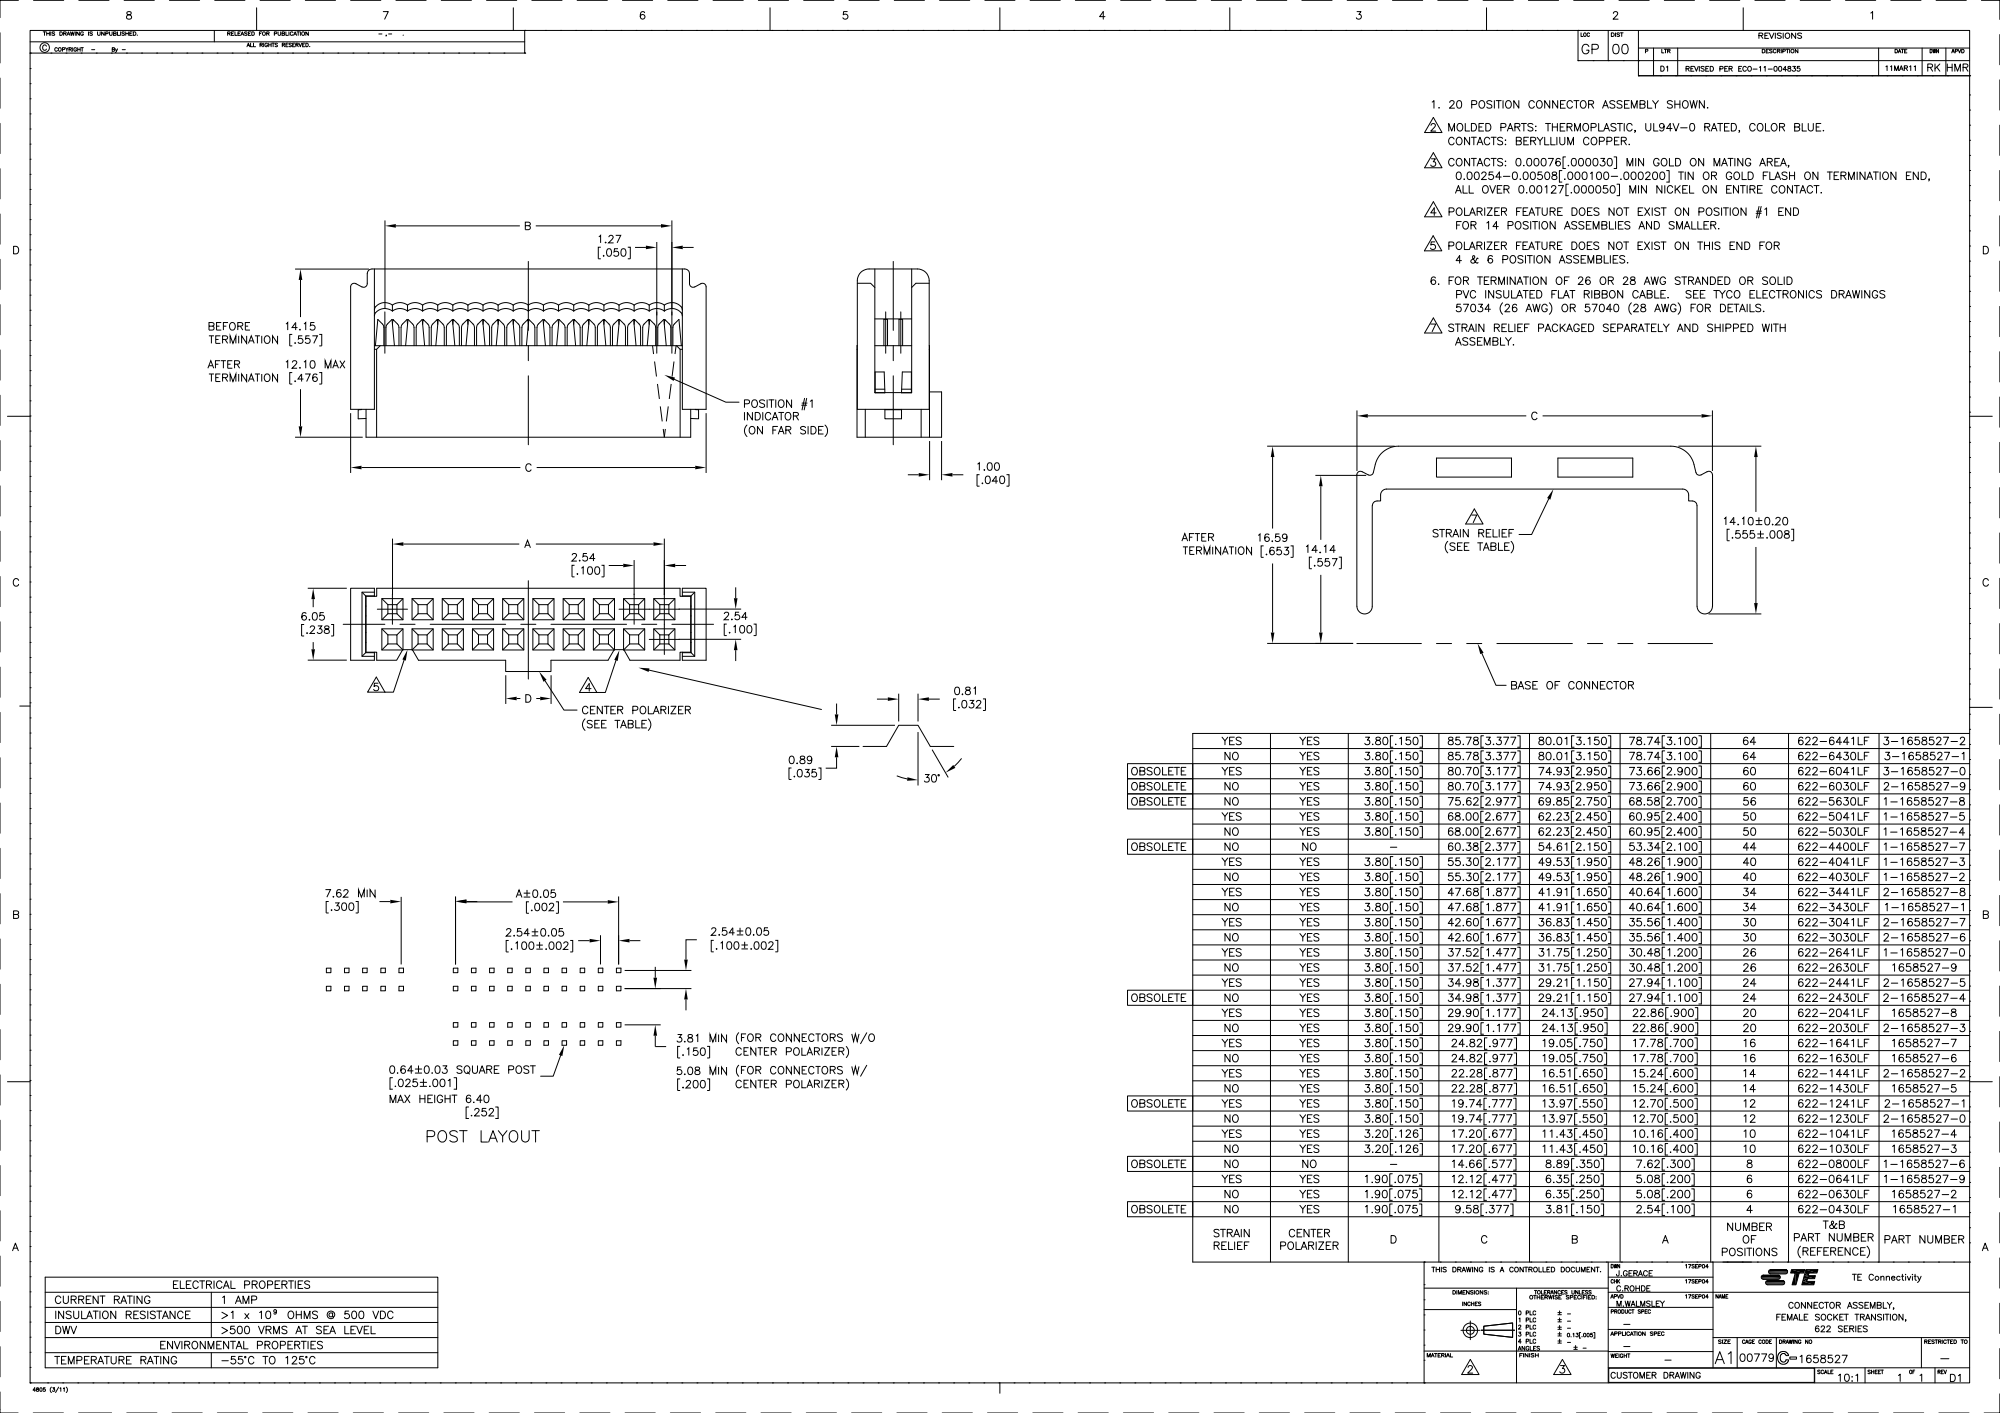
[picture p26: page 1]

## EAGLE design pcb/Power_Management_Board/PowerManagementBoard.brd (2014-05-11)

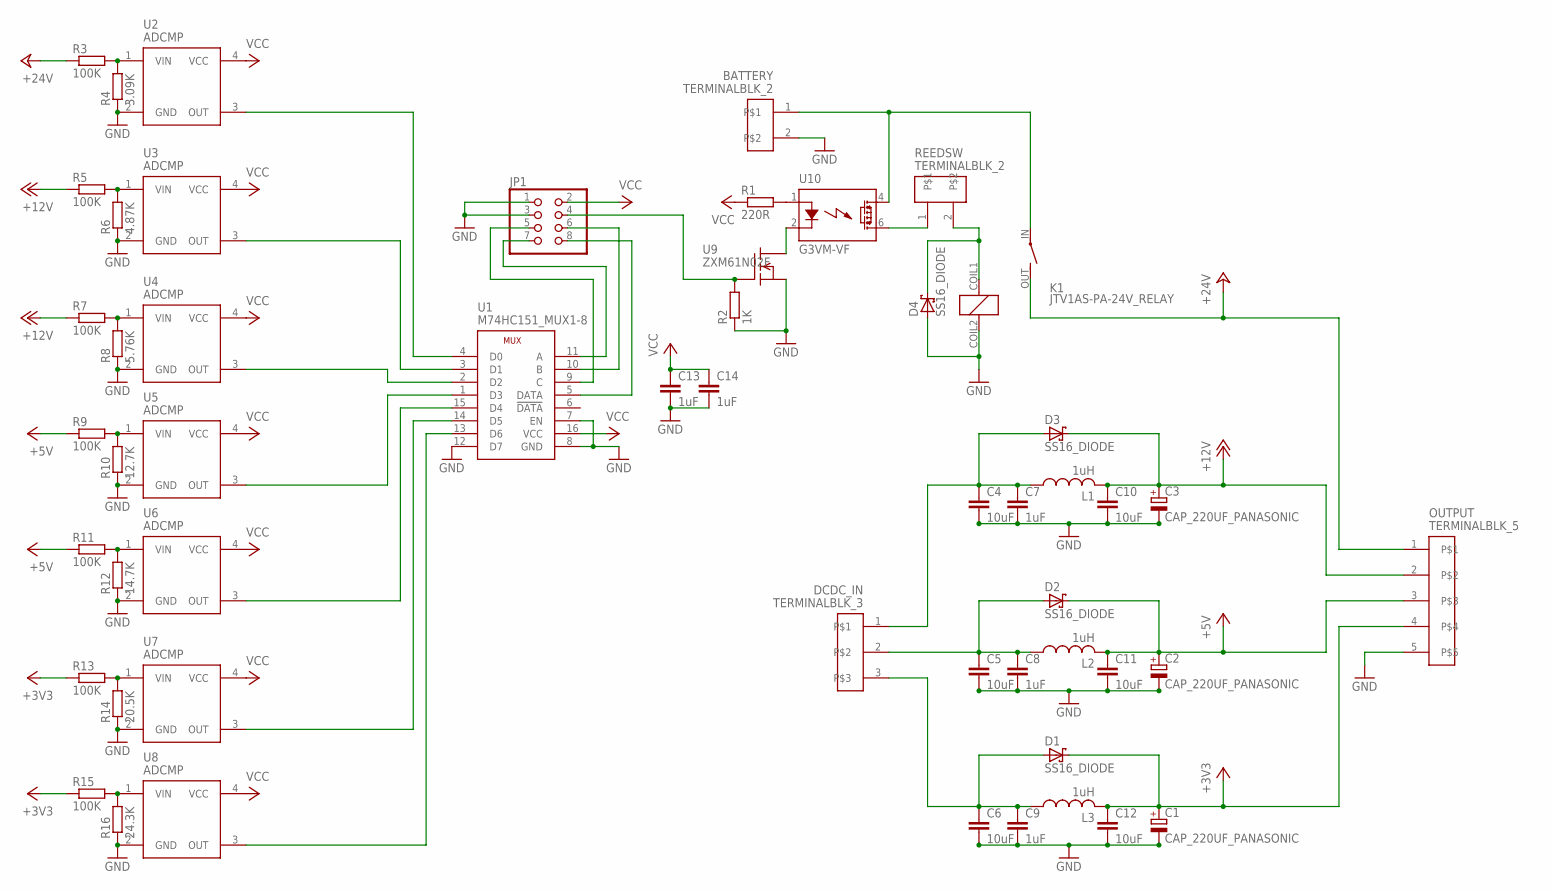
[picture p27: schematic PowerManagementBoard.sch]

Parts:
BATTERY: TERMINALBLK_2; TERMINAL_BLK-2
C1, C2, C3: CAP_220UF_PANASONIC
C4, C5, C6, C10, C11, C12: 10uF; C1206
C7, C8, C9, C13, C14: 1uF; C1206
D1, D2, D3, D4: SS16_DIODE; DO214AC
DCDC_IN: TERMINALBLK_3; TERMINAL_BLK-3
JP1: PINHD-2X4; 2X04
K1: JTV1AS-PA-24V_RELAY; JTV-RELAY_FORM1A
L1, L2, L3: 1uH; CHOKE_WE-HCC_8070
OUTPUT: TERMINALBLK_5; TERMINAL_BLK-5
R1: 220R; R0603
R2: 1K; R0603
R3, R5, R7, R9, R11, R13, R15: 100K; R0603
R4: 3.09K; R0603
R6: 4.87K; R0603
R8: 5.76K; R0603
R10: 12.7K; R0603
R12: 14.7K; R0603
R14: 20.5K; R0603
R16: 24.3K; R0603
REEDSW: TERMINALBLK_2; TERMINAL_BLK-2
U1: M74HC151_MUX1-8; TSSOP16
U2, U3, U4, U5, U6, U7, U8: ADCMP; SC70-4
U9: ZXM61N02F; SOT23W
U10: G3VM-VF

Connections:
+3V3: C1.P (+), C12.1, D1.C, L3.P$2 (2), OUTPUT.4, R13.1, R15.1
+5V: C2.P (+), C11.1, D2.C, L2.P$2 (2), OUTPUT.3, R9.1, R11.1
+12V: C3.P (+), C10.1, D3.C, L1.P$2 (2), OUTPUT.2, R5.1, R7.1
+24V: K1.OUT (S), OUTPUT.1, R3.1
GND: BATTERY.2, C1.N (-), C2.N (-), C3.N (-), C4.2, C5.2, C6.2, C7.2, C8.2, C9.2, C10.2, C11.2, C12.2, C13.2, C14.2, D4.A, JP1.1, JP1.3, K1.COIL2 (2), OUTPUT.5, R2.1, R4.1, R6.1, R8.1, R10.1, R12.1, R14.1, R16.1, U1.7 (EN), U1.8 (GND), U1.12 (D7), U2.2 (GND), U3.2 (GND), U4.2 (GND), U5.2 (GND), U6.2 (GND), U7.2 (GND), U8.2 (GND), U9.2 (S)
unnamed: BATTERY.1, K1.IN, U10.4 (DS1)
unnamed: REEDSW.1, U10.6 (DS2)
unnamed: D4.C, K1.COIL1 (1), REEDSW.2
unnamed: C6.1, C9.1, D1.A, DCDC_IN.3, L3.P$1 (1)
unnamed: C5.1, C8.1, D2.A, DCDC_IN.2, L2.P$1 (1)
unnamed: C4.1, C7.1, D3.A, DCDC_IN.1, L1.P$1 (1)
unnamed: U9.3 (D), U10.2 (K)
unnamed: R1.2, U10.1 (A)
unnamed: JP1.4, R2.2, U9.1 (G)
unnamed: JP1.8, U1.5 (DATA)
unnamed: JP1.6, U1.10 (B)
unnamed: JP1.7, U1.11 (A)
unnamed: JP1.5, U1.9 (C)
unnamed: R3.2, R4.2, U2.1 (VIN)
unnamed: R5.2, R6.2, U3.1 (VIN)
unnamed: R7.2, R8.2, U4.1 (VIN)
unnamed: R9.2, R10.2, U5.1 (VIN)
unnamed: R11.2, R12.2, U6.1 (VIN)
unnamed: R13.2, R14.2, U7.1 (VIN)
unnamed: R15.2, R16.2, U8.1 (VIN)
unnamed: U1.4 (D0), U2.3 (OUT)
unnamed: U1.3 (D1), U3.3 (OUT)
unnamed: U1.2 (D2), U4.3 (OUT)
unnamed: U1.1 (D3), U5.3 (OUT)
unnamed: U1.15 (D4), U6.3 (OUT)
unnamed: U1.14 (D5), U7.3 (OUT)
unnamed: U1.13 (D6), U8.3 (OUT)
VCC: C13.1, C14.1, JP1.2, R1.1, U1.16 (VCC), U2.4 (VCC), U3.4 (VCC), U4.4 (VCC), U5.4 (VCC), U6.4 (VCC), U7.4 (VCC), U8.4 (VCC)

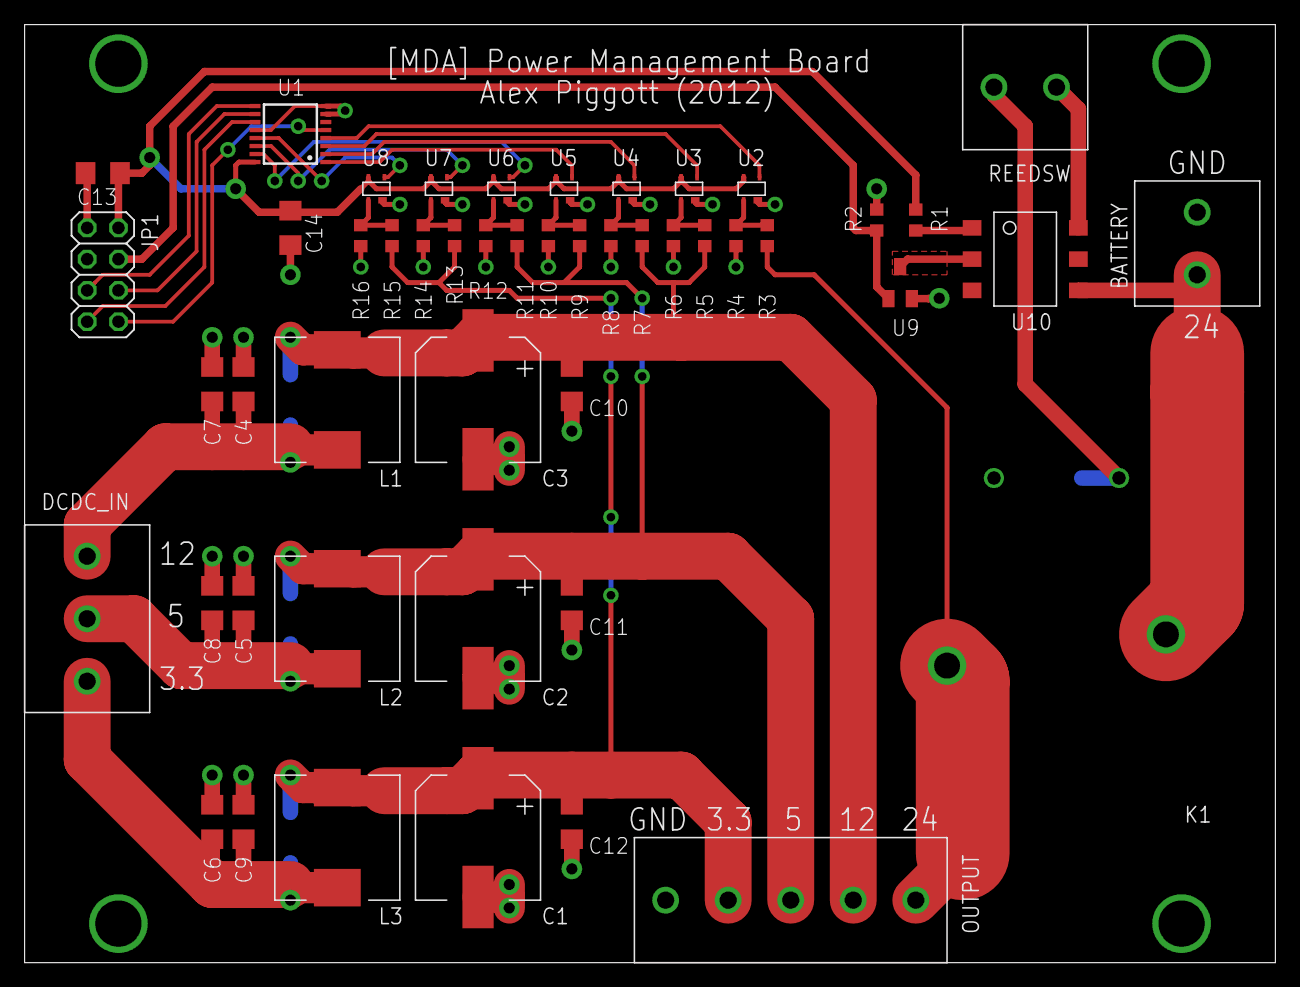
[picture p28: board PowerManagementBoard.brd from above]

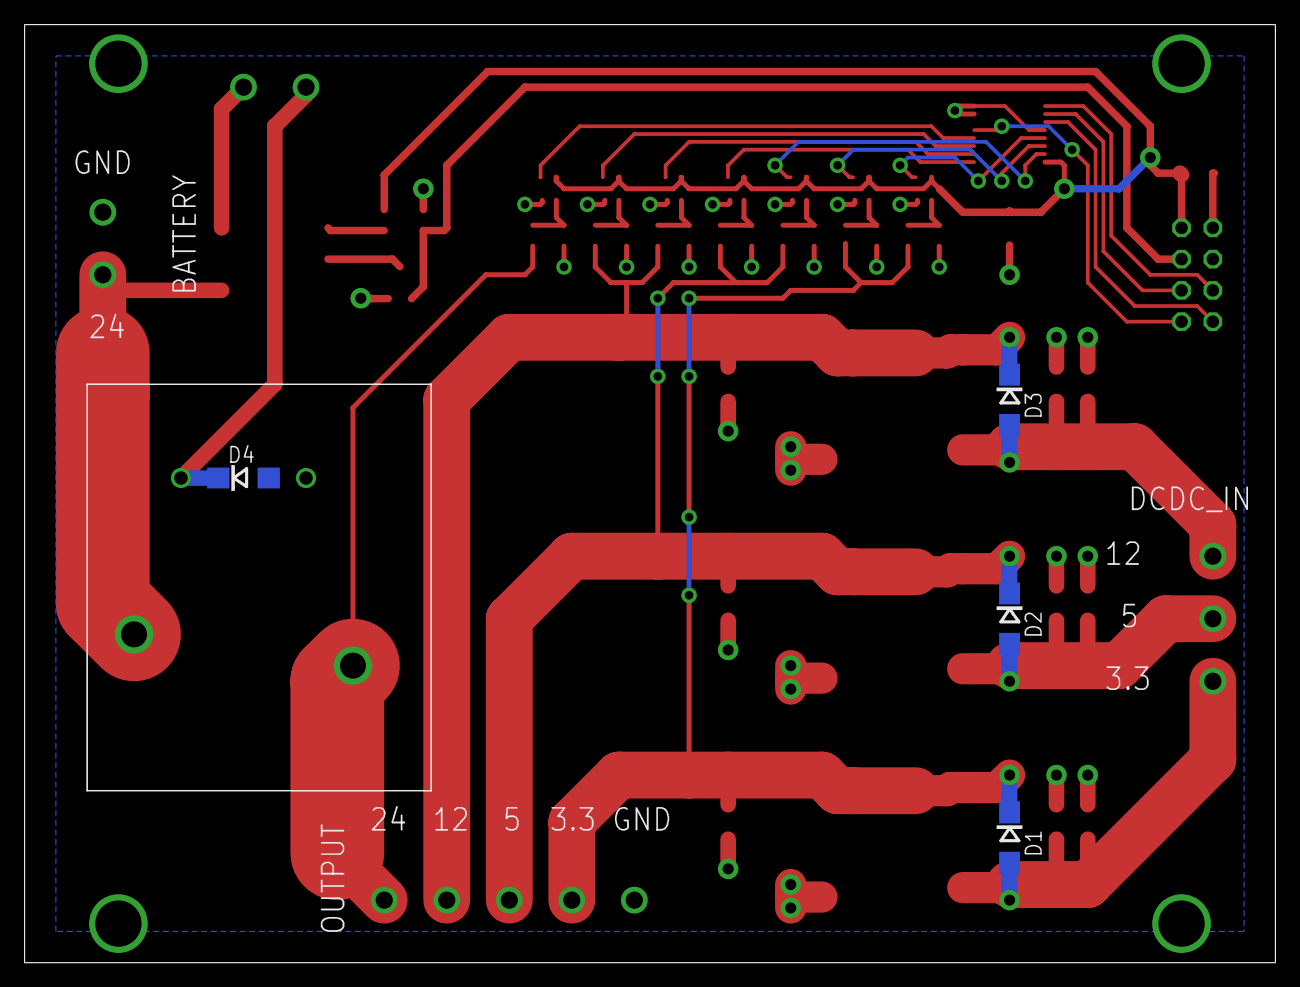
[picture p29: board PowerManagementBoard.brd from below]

Board: 2 copper layers, 101.6 x 76.2 mm, 53 parts (4 on the bottom side), 33 nets.

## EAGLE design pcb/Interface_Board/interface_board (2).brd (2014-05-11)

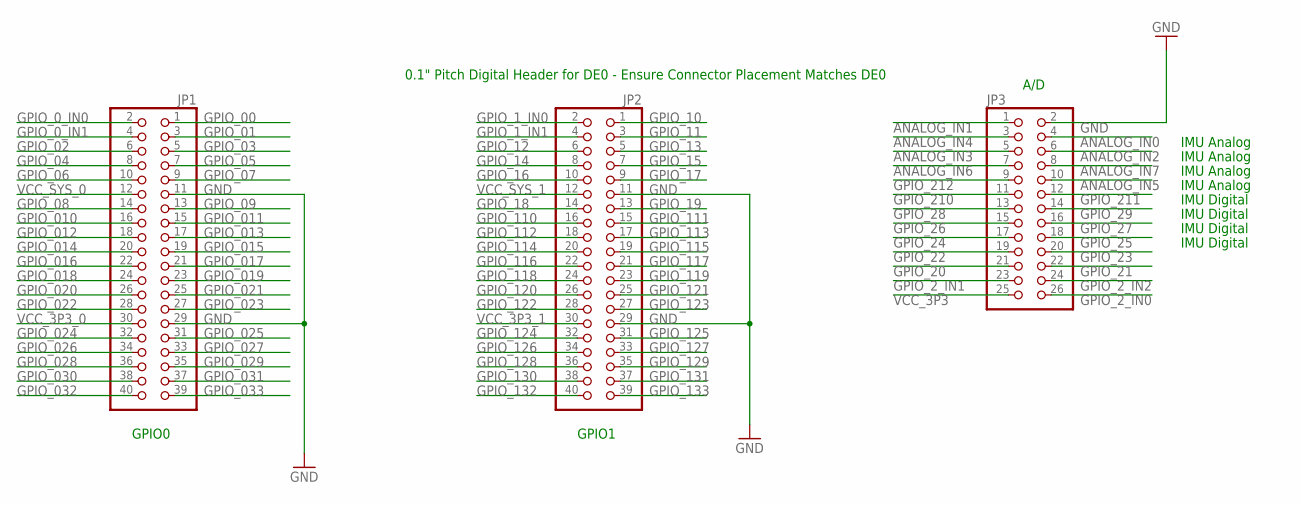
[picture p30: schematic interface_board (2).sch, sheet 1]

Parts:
JP1, JP2: PINHD-2X20; 2X20
JP3: PINHD-2X13; 2X13

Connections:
ANALOG_IN0: JP3.4; also elsewhere on the board
ANALOG_IN1: JP3.1; also elsewhere on the board
ANALOG_IN2: JP3.6; also elsewhere on the board
ANALOG_IN3: JP3.5; also elsewhere on the board
ANALOG_IN4: JP3.3; also elsewhere on the board
ANALOG_IN5: JP3.10; also elsewhere on the board
ANALOG_IN6: JP3.7; also elsewhere on the board
ANALOG_IN7: JP3.8; also elsewhere on the board
GND: JP1.11, JP1.29, JP2.11, JP2.29, JP3.2; also elsewhere on the board
GPIO_00: JP1.1; also elsewhere on the board
GPIO_0_IN0: JP1.2; also elsewhere on the board
GPIO_0_IN1: JP1.4; also elsewhere on the board
GPIO_01: JP1.3; also elsewhere on the board
GPIO_1_IN0: JP2.2; also elsewhere on the board
GPIO_1_IN1: JP2.4; also elsewhere on the board
GPIO_02: JP1.6; also elsewhere on the board
GPIO_2_IN0: JP3.26; also elsewhere on the board
GPIO_2_IN1: JP3.23; also elsewhere on the board
GPIO_2_IN2: JP3.24; also elsewhere on the board
GPIO_03: JP1.5; also elsewhere on the board
GPIO_04: JP1.8; also elsewhere on the board
GPIO_05: JP1.7; also elsewhere on the board
GPIO_06: JP1.10; also elsewhere on the board
GPIO_07: JP1.9; also elsewhere on the board
GPIO_08: JP1.14; also elsewhere on the board
GPIO_09: JP1.13; also elsewhere on the board
GPIO_010: JP1.16; also elsewhere on the board
GPIO_10: JP2.1; also elsewhere on the board
GPIO_011: JP1.15; also elsewhere on the board
GPIO_11: JP2.3; also elsewhere on the board
GPIO_012: JP1.18; also elsewhere on the board
GPIO_12: JP2.6; also elsewhere on the board
GPIO_013: JP1.17; also elsewhere on the board
GPIO_13: JP2.5; also elsewhere on the board
GPIO_014: JP1.20; also elsewhere on the board
GPIO_14: JP2.8; also elsewhere on the board
GPIO_015: JP1.19; also elsewhere on the board
GPIO_15: JP2.7; also elsewhere on the board
GPIO_016: JP1.22; also elsewhere on the board
GPIO_16: JP2.10; also elsewhere on the board
GPIO_017: JP1.21; also elsewhere on the board
GPIO_17: JP2.9; also elsewhere on the board
GPIO_018: JP1.24; also elsewhere on the board
GPIO_18: JP2.14; also elsewhere on the board
GPIO_019: JP1.23; also elsewhere on the board
GPIO_19: JP2.13; also elsewhere on the board
GPIO_020: JP1.26; also elsewhere on the board
GPIO_20: JP3.21; also elsewhere on the board
GPIO_021: JP1.25; also elsewhere on the board
GPIO_21: JP3.22; also elsewhere on the board
GPIO_022: JP1.28; also elsewhere on the board
GPIO_22: JP3.19; also elsewhere on the board
GPIO_023: JP1.27; also elsewhere on the board
GPIO_23: JP3.20; also elsewhere on the board
GPIO_024: JP1.32; also elsewhere on the board
GPIO_24: JP3.17; also elsewhere on the board
GPIO_025: JP1.31; also elsewhere on the board
GPIO_25: JP3.18; also elsewhere on the board
GPIO_026: JP1.34; also elsewhere on the board
GPIO_26: JP3.15; also elsewhere on the board
GPIO_027: JP1.33; also elsewhere on the board
GPIO_27: JP3.16; also elsewhere on the board
GPIO_028: JP1.36; also elsewhere on the board
GPIO_28: JP3.13; also elsewhere on the board
GPIO_029: JP1.35; also elsewhere on the board
GPIO_29: JP3.14; also elsewhere on the board
GPIO_030: JP1.38; also elsewhere on the board
GPIO_031: JP1.37; also elsewhere on the board
GPIO_032: JP1.40; also elsewhere on the board
GPIO_033: JP1.39; also elsewhere on the board
GPIO_110: JP2.16; also elsewhere on the board
GPIO_111: JP2.15; also elsewhere on the board
GPIO_112: JP2.18; also elsewhere on the board
GPIO_113: JP2.17; also elsewhere on the board
GPIO_114: JP2.20; also elsewhere on the board
GPIO_115: JP2.19; also elsewhere on the board
GPIO_116: JP2.22; also elsewhere on the board
GPIO_117: JP2.21; also elsewhere on the board
GPIO_118: JP2.24; also elsewhere on the board
GPIO_119: JP2.23; also elsewhere on the board
GPIO_120: JP2.26; also elsewhere on the board
GPIO_121: JP2.25; also elsewhere on the board
GPIO_122: JP2.28; also elsewhere on the board
GPIO_123: JP2.27; also elsewhere on the board
GPIO_124: JP2.32; also elsewhere on the board
GPIO_125: JP2.31; also elsewhere on the board
GPIO_126: JP2.34; also elsewhere on the board
GPIO_127: JP2.33; also elsewhere on the board
GPIO_128: JP2.36; also elsewhere on the board
GPIO_129: JP2.35; also elsewhere on the board
GPIO_130: JP2.38; also elsewhere on the board
GPIO_131: JP2.37; also elsewhere on the board
GPIO_132: JP2.40; also elsewhere on the board
GPIO_133: JP2.39; also elsewhere on the board
GPIO_210: JP3.11; also elsewhere on the board
GPIO_211: JP3.12; also elsewhere on the board
GPIO_212: JP3.9; also elsewhere on the board
VCC_3P3: JP3.25; also elsewhere on the board
VCC_3P3_0: JP1.30
VCC_3P3_1: JP2.30; also elsewhere on the board
VCC_SYS_0: JP1.12
VCC_SYS_1: JP2.12

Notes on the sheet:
0.1" Pitch Digital Header for DE0 - Ensure Connector Placement Matches DE0
GPIO0
GPIO1
A/D
IMU Analog
IMU Digital

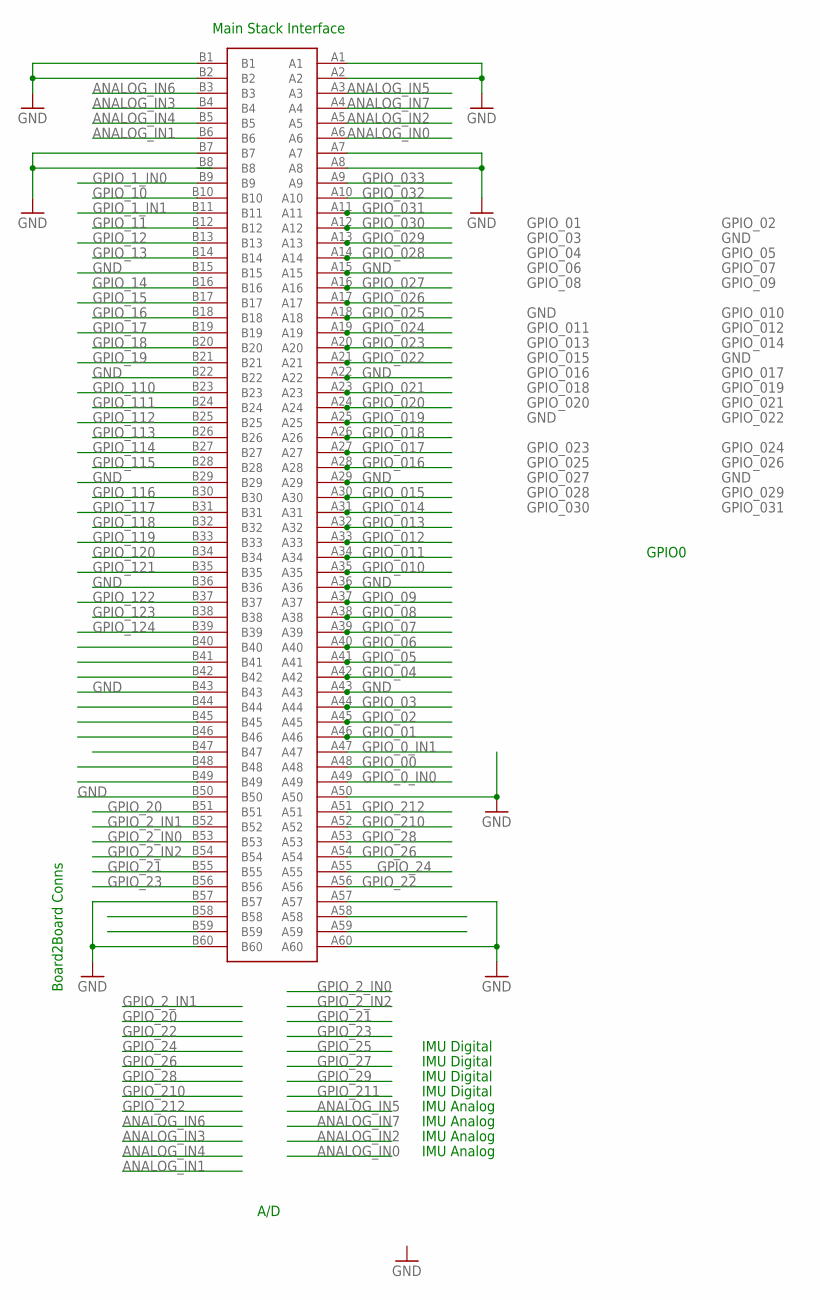
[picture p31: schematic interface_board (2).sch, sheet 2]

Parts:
U$10: MAIN-STACK-CONN-WIDEPITCH; STACK-CONN-WIDEPITCH

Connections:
ANALOG_IN0: U$10.A6; also elsewhere on the board
ANALOG_IN1: U$10.B6; also elsewhere on the board
ANALOG_IN2: U$10.A5; also elsewhere on the board
ANALOG_IN3: U$10.B4; also elsewhere on the board
ANALOG_IN4: U$10.B5; also elsewhere on the board
ANALOG_IN5: U$10.A3; also elsewhere on the board
ANALOG_IN6: U$10.B3; also elsewhere on the board
ANALOG_IN7: U$10.A4; also elsewhere on the board
GND: U$10.A1, U$10.A2, U$10.A7, U$10.A8, U$10.A15, U$10.A22, U$10.A29, U$10.A36, U$10.A43, U$10.A50, U$10.A57, U$10.A60, U$10.B1, U$10.B2, U$10.B7, U$10.B15, U$10.B22, U$10.B29, U$10.B36, U$10.B43, U$10.B50, U$10.B57, U$10.B60; also elsewhere on the board
GPIO_00: U$10.A48; also elsewhere on the board
GPIO_0_IN0: U$10.A49; also elsewhere on the board
GPIO_0_IN1: U$10.A47; also elsewhere on the board
GPIO_01: U$10.A46; also elsewhere on the board
GPIO_1_IN0: U$10.B9; also elsewhere on the board
GPIO_1_IN1: U$10.B11; also elsewhere on the board
GPIO_02: U$10.A45; also elsewhere on the board
GPIO_2_IN0: U$10.B53; also elsewhere on the board
GPIO_2_IN1: U$10.B52; also elsewhere on the board
GPIO_2_IN2: U$10.B54; also elsewhere on the board
GPIO_03: U$10.A44; also elsewhere on the board
GPIO_04: U$10.A42; also elsewhere on the board
GPIO_05: U$10.A41; also elsewhere on the board
GPIO_06: U$10.A40; also elsewhere on the board
GPIO_07: U$10.A39; also elsewhere on the board
GPIO_08: U$10.A38; also elsewhere on the board
GPIO_09: U$10.A37; also elsewhere on the board
GPIO_010: U$10.A35; also elsewhere on the board
GPIO_10: U$10.B10; also elsewhere on the board
GPIO_011: U$10.A34; also elsewhere on the board
GPIO_11: U$10.B12; also elsewhere on the board
GPIO_012: U$10.A33; also elsewhere on the board
GPIO_12: U$10.B13; also elsewhere on the board
GPIO_013: U$10.A32; also elsewhere on the board
GPIO_13: U$10.B14; also elsewhere on the board
GPIO_014: U$10.A31; also elsewhere on the board
GPIO_14: U$10.B16; also elsewhere on the board
GPIO_015: U$10.A30; also elsewhere on the board
GPIO_15: U$10.B17; also elsewhere on the board
GPIO_016: U$10.A28; also elsewhere on the board
GPIO_16: U$10.B18; also elsewhere on the board
GPIO_017: U$10.A27; also elsewhere on the board
GPIO_17: U$10.B19; also elsewhere on the board
GPIO_018: U$10.A26; also elsewhere on the board
GPIO_18: U$10.B20; also elsewhere on the board
GPIO_019: U$10.A25; also elsewhere on the board
GPIO_19: U$10.B21; also elsewhere on the board
GPIO_020: U$10.A24; also elsewhere on the board
GPIO_20: U$10.B51; also elsewhere on the board
GPIO_021: U$10.A23; also elsewhere on the board
GPIO_21: U$10.B55; also elsewhere on the board
GPIO_022: U$10.A21; also elsewhere on the board
GPIO_22: U$10.A56; also elsewhere on the board
GPIO_023: U$10.A20; also elsewhere on the board
GPIO_23: U$10.B56; also elsewhere on the board
GPIO_024: U$10.A19; also elsewhere on the board
GPIO_24: U$10.A55; also elsewhere on the board
GPIO_025: U$10.A18; also elsewhere on the board
GPIO_026: U$10.A17; also elsewhere on the board
GPIO_26: U$10.A54; also elsewhere on the board
GPIO_027: U$10.A16; also elsewhere on the board
GPIO_028: U$10.A14; also elsewhere on the board
GPIO_28: U$10.A53; also elsewhere on the board
GPIO_029: U$10.A13; also elsewhere on the board
GPIO_030: U$10.A12; also elsewhere on the board
GPIO_031: U$10.A11; also elsewhere on the board
GPIO_032: U$10.A10; also elsewhere on the board
GPIO_033: U$10.A9; also elsewhere on the board
GPIO_110: U$10.B23; also elsewhere on the board
GPIO_111: U$10.B24; also elsewhere on the board
GPIO_112: U$10.B25; also elsewhere on the board
GPIO_113: U$10.B26; also elsewhere on the board
GPIO_114: U$10.B27; also elsewhere on the board
GPIO_115: U$10.B28; also elsewhere on the board
GPIO_116: U$10.B30; also elsewhere on the board
GPIO_117: U$10.B31; also elsewhere on the board
GPIO_118: U$10.B32; also elsewhere on the board
GPIO_119: U$10.B33; also elsewhere on the board
GPIO_120: U$10.B34; also elsewhere on the board
GPIO_121: U$10.B35; also elsewhere on the board
GPIO_122: U$10.B37; also elsewhere on the board
GPIO_123: U$10.B38; also elsewhere on the board
GPIO_124: U$10.B39; also elsewhere on the board
GPIO_210: U$10.A52; also elsewhere on the board
GPIO_212: U$10.A51; also elsewhere on the board

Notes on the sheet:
Main Stack Interface
GPIO0
A/D
IMU Analog
IMU Digital
Board2Board Conns

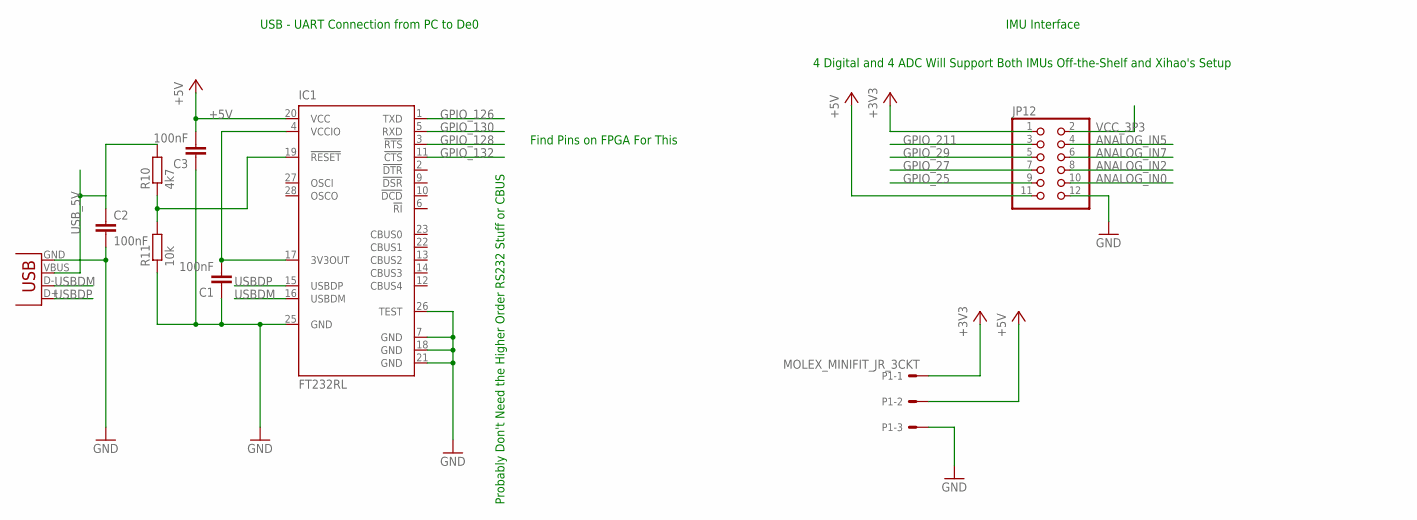
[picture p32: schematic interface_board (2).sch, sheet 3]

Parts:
C1, C2, C3: 100nF; C0805
IC1: FT232RL; SSOP28
JP12: PINHD-2X6; 2X06
P1: MOLEX_MINIFIT_JR_3CKT; 3CKT_MINIFIT_JR
R10: 4k7; M0805
R11: 10k; M0805
X1: USBSMD; USB-MINIB

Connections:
+3V3: JP12.1, P1.1; also elsewhere on the board
+5V: C3.2, IC1.20 (VCC), JP12.11, P1.2
ANALOG_IN0: JP12.10; also elsewhere on the board
ANALOG_IN2: JP12.8; also elsewhere on the board
ANALOG_IN5: JP12.4; also elsewhere on the board
ANALOG_IN7: JP12.6; also elsewhere on the board
GND: C1.1, C2.2, C3.1, IC1.7 (GND), IC1.18 (GND), IC1.21 (GND), IC1.25 (GND), IC1.26 (TEST), JP12.12, P1.3, R11.1, X1.GND; also elsewhere on the board
GPIO_25: JP12.9; also elsewhere on the board
GPIO_27: JP12.7; also elsewhere on the board
GPIO_29: JP12.5; also elsewhere on the board
GPIO_126: IC1.1 (TXD); also elsewhere on the board
GPIO_128: IC1.3 (!RTS); also elsewhere on the board
GPIO_130: IC1.5 (RXD); also elsewhere on the board
GPIO_132: IC1.11 (!CTS); also elsewhere on the board
GPIO_211: JP12.3; also elsewhere on the board
unnamed: C1.2, IC1.4 (VCCIO), IC1.17 (3V3OUT)
unnamed: IC1.19 (!RESET), R10.1, R11.2
USBDM: IC1.16 (USBDM), X1.D-
USBDP: IC1.15 (USBDP), X1.D+
USB_5V: C2.1, R10.2, X1.VBUS
VCC_3P3: JP12.2; also elsewhere on the board

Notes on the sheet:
USB - UART Connection from PC to De0
IMU Interface
Probably Don't Need the Higher Order RS232 Stuff or CBUS
Find Pins on FPGA For This
4 Digital and 4 ADC Will Support Both IMUs Off-the-Shelf and Xihao's Setup

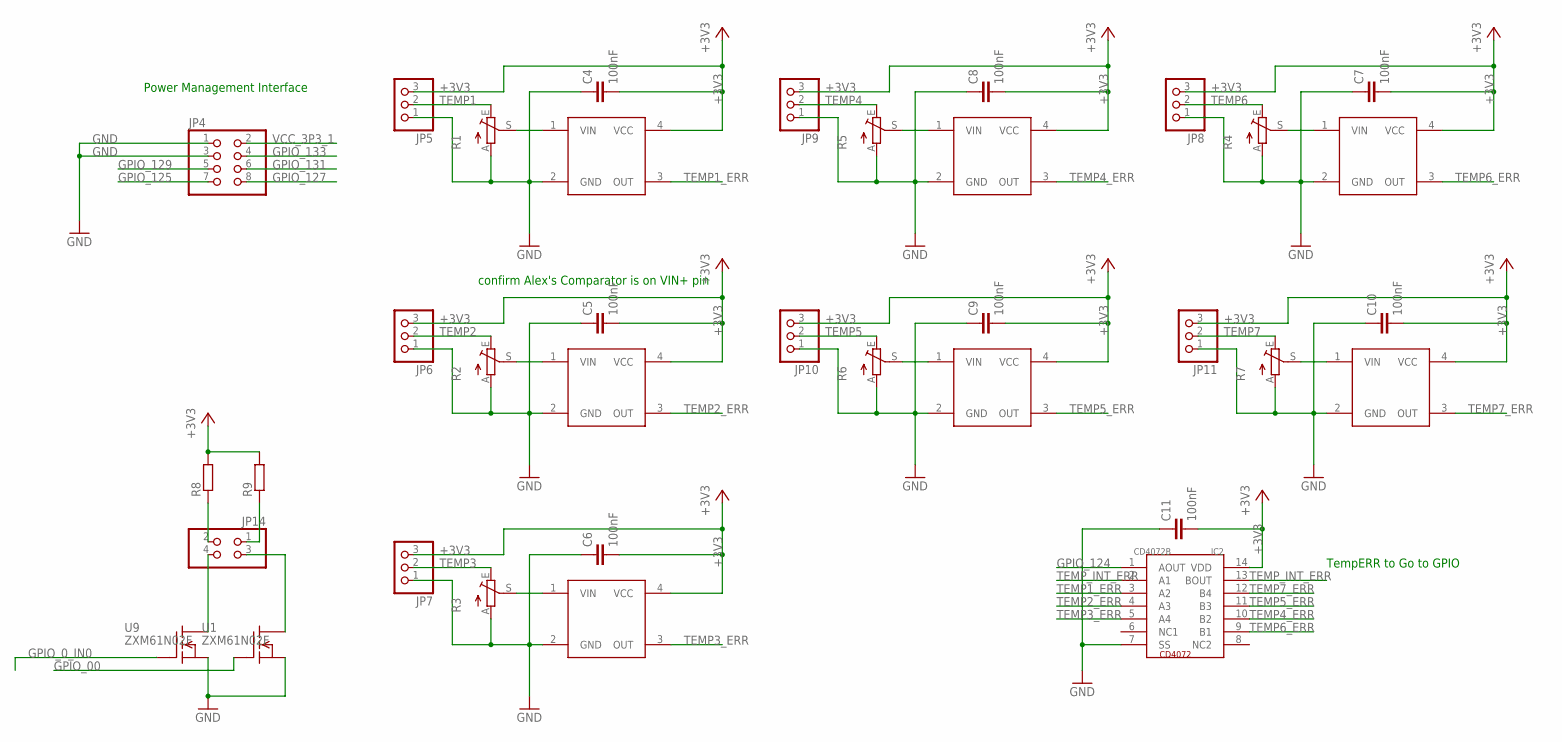
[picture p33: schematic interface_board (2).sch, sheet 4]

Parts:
C4, C5, C6, C7, C8, C9, C10, C11: 100nF; C0805
IC2: CD4072B; SO14
JP4: PINHD-2X4; 2X04
JP5, JP6, JP7, JP8, JP9, JP10, JP11: PINHD-1X3; 1X03
JP14: PINHD-2X2; 2X02
R1, R2, R3, R4, R5, R6, R7: TRIM_1234-S64YW; POT
R8, R9: R-EU_M1206; M1206
U1, U9: ZXM61N02F; SOT23W
U$2, U$4, U$5, U$6, U$7, U$8, U$9: ADCMP

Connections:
+3V3: C4.2, C5.2, C6.2, C7.2, C8.2, C9.2, C10.2, C11.2, IC2.14 (VDD), JP5.3, JP6.3, JP7.3, JP8.3, JP9.3, JP10.3, JP11.3, R8.2, R9.2, U$2.4 (VCC), U$4.4 (VCC), U$5.4 (VCC), U$6.4 (VCC), U$7.4 (VCC), U$8.4 (VCC), U$9.4 (VCC); also elsewhere on the board
GND: C4.1, C5.1, C6.1, C7.1, C8.1, C9.1, C10.1, C11.1, IC2.7 (SS), JP4.1, JP4.3, JP5.1, JP6.1, JP7.1, JP8.1, JP9.1, JP10.1, JP11.1, R1.A, R2.A, R3.A, R4.A, R5.A, R6.A, R7.A, U1.2 (S), U9.2 (S), U$2.2 (GND), U$4.2 (GND), U$5.2 (GND), U$6.2 (GND), U$7.2 (GND), U$8.2 (GND), U$9.2 (GND); also elsewhere on the board
GPIO_00: U1.1 (G); also elsewhere on the board
GPIO_0_IN0: U9.1 (G); also elsewhere on the board
GPIO_124: IC2.1 (AOUT); also elsewhere on the board
GPIO_125: JP4.7; also elsewhere on the board
GPIO_127: JP4.8; also elsewhere on the board
GPIO_129: JP4.5; also elsewhere on the board
GPIO_131: JP4.6; also elsewhere on the board
GPIO_133: JP4.4; also elsewhere on the board
unnamed: R1.S, U$2.1 (VIN)
unnamed: R2.S, U$4.1 (VIN)
unnamed: R3.S, U$5.1 (VIN)
unnamed: R4.S, U$6.1 (VIN)
unnamed: R5.S, U$7.1 (VIN)
unnamed: R6.S, U$8.1 (VIN)
unnamed: R7.S, U$9.1 (VIN)
unnamed: JP14.2, R8.1
unnamed: JP14.4, U9.3 (D)
unnamed: JP14.1, R9.1
unnamed: JP14.3, U1.3 (D)
TEMP1: JP5.2, R1.E
TEMP1_ERR: IC2.3 (A2), U$2.3 (OUT)
TEMP2: JP6.2, R2.E
TEMP2_ERR: IC2.4 (A3), U$4.3 (OUT)
TEMP3: JP7.2, R3.E
TEMP3_ERR: IC2.5 (A4), U$5.3 (OUT)
TEMP4: JP9.2, R5.E
TEMP4_ERR: IC2.10 (B2), U$7.3 (OUT)
TEMP5: JP10.2, R6.E
TEMP5_ERR: IC2.11 (B3), U$8.3 (OUT)
TEMP6: JP8.2, R4.E
TEMP6_ERR: IC2.9 (B1), U$6.3 (OUT)
TEMP7: JP11.2, R7.E
TEMP7_ERR: IC2.12 (B4), U$9.3 (OUT)
TEMP_INT_ERR: IC2.2 (A1), IC2.13 (BOUT)
VCC_3P3_1: JP4.2; also elsewhere on the board

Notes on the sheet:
Power Management Interface
TempERR to Go to GPIO
confirm Alex's Comparator is on VIN+ pin

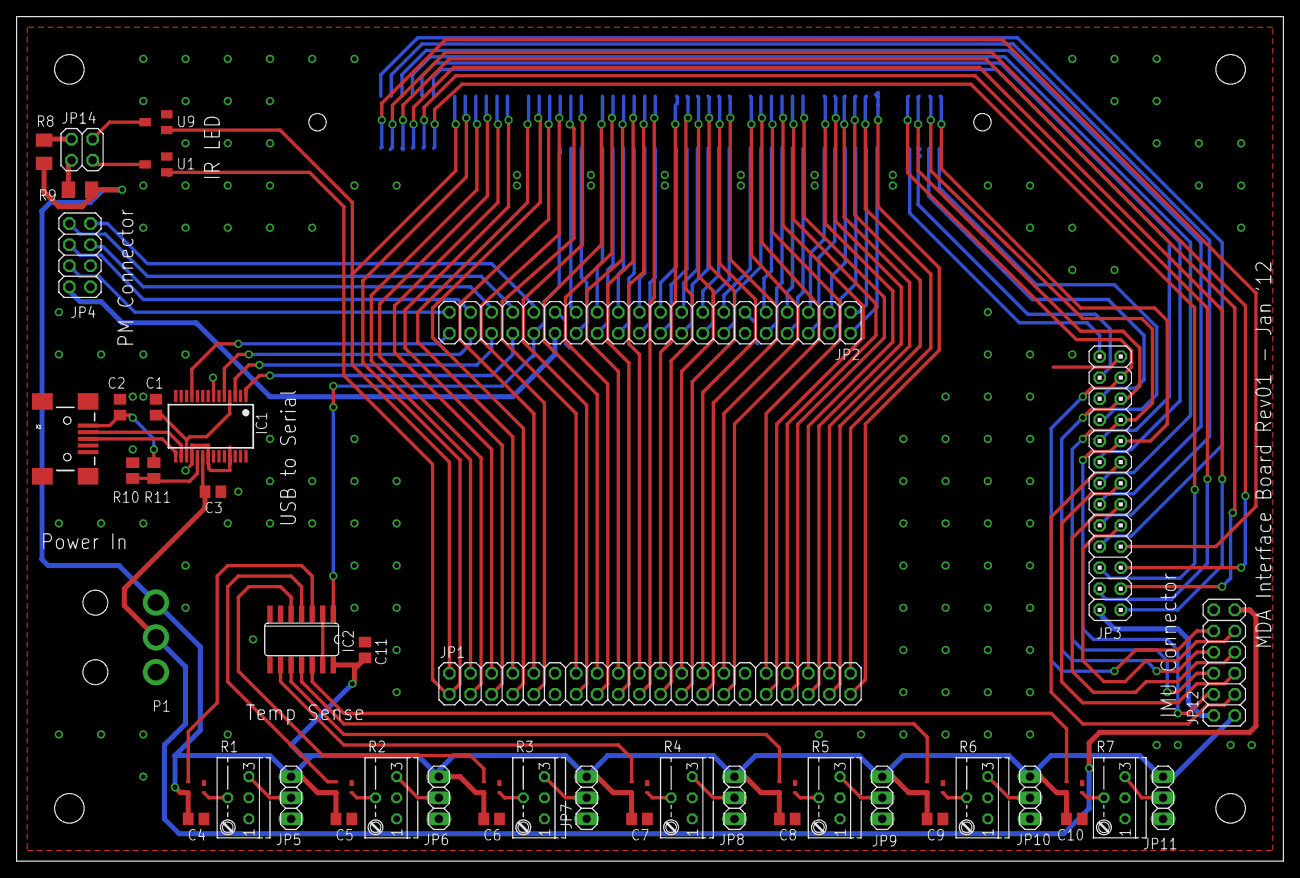
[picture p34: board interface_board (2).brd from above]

Board: 2 copper layers, 152.4 x 101.6 mm, 49 parts (1 on the bottom side), 132 nets.

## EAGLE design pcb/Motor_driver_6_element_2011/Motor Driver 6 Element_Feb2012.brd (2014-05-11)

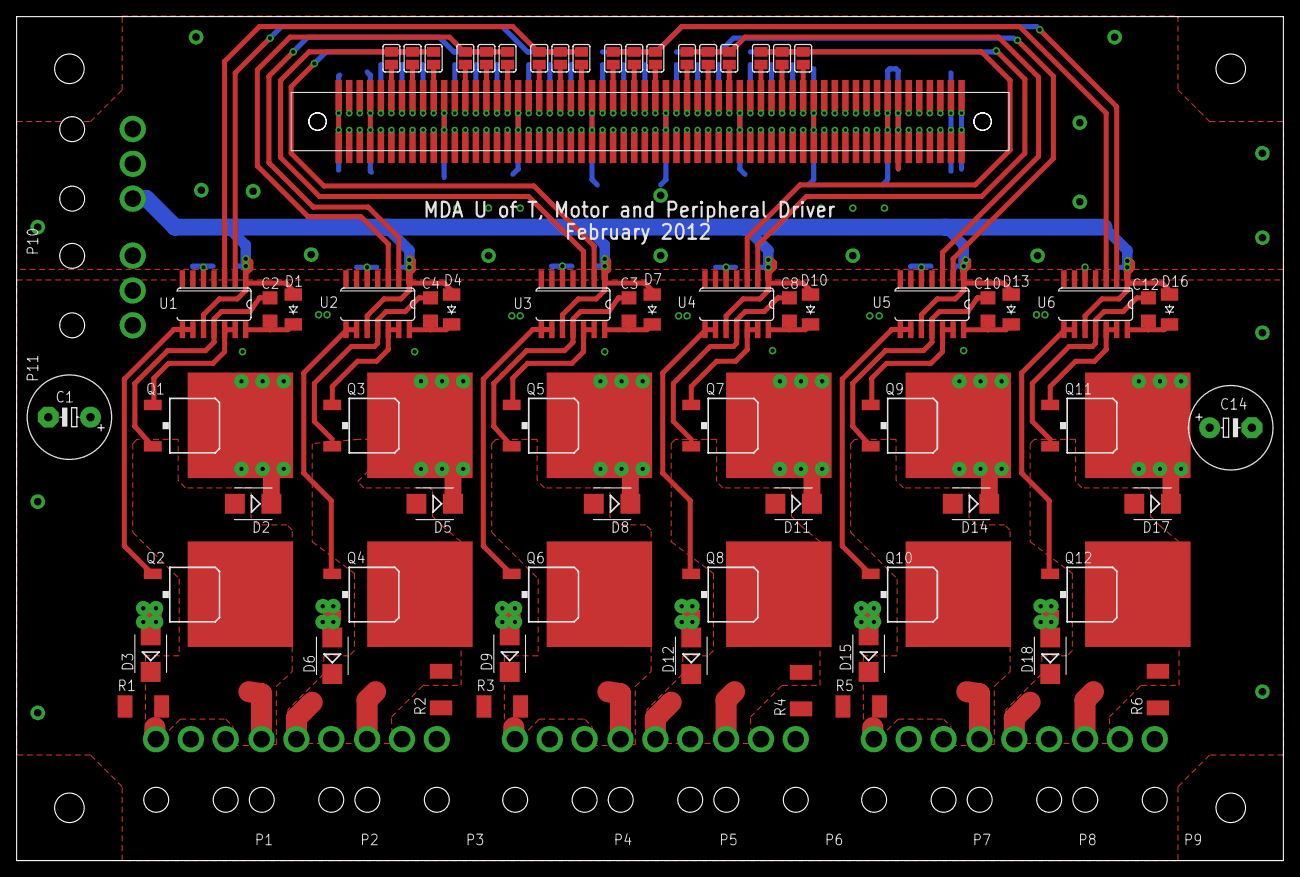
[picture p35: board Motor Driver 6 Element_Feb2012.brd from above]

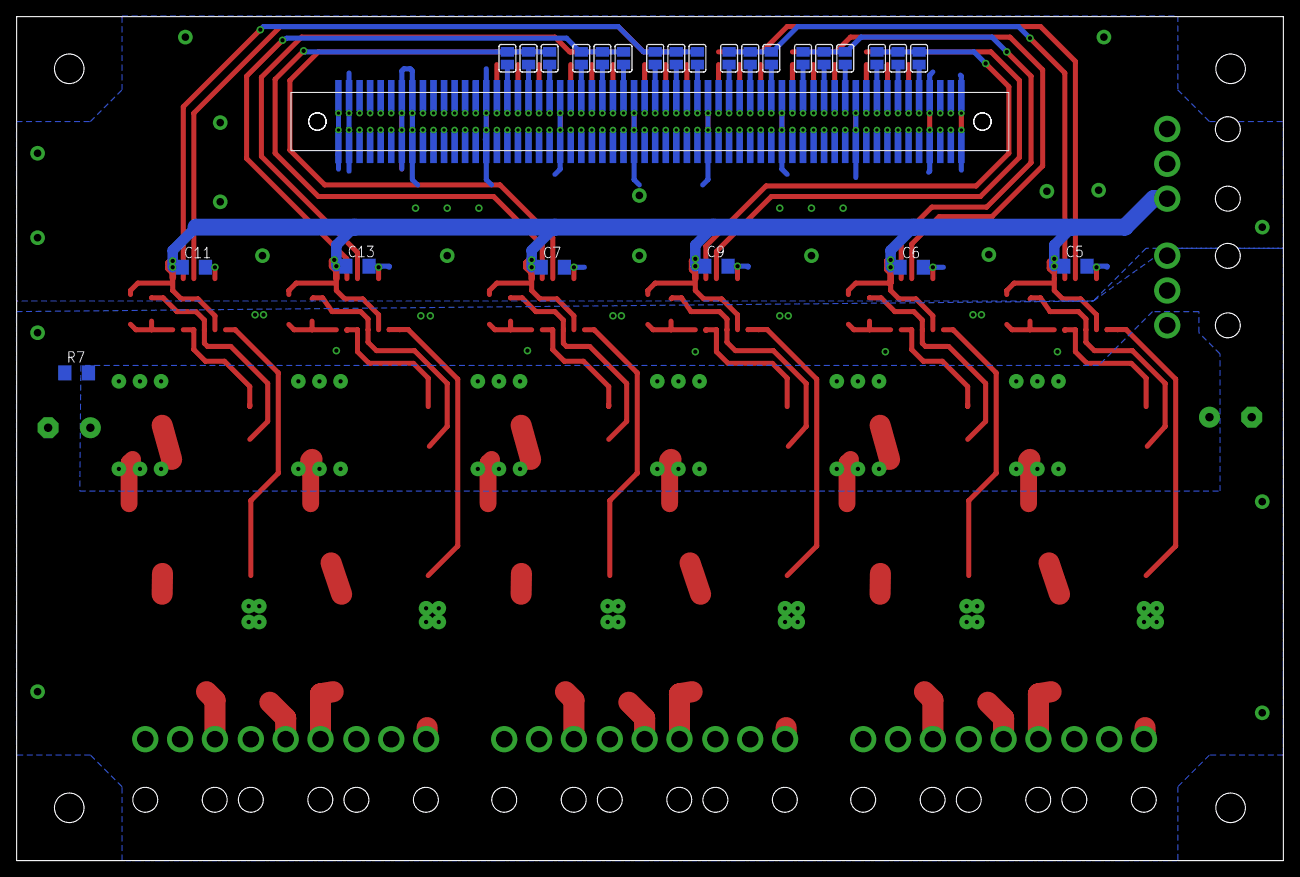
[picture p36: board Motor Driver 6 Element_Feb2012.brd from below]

Board: 2 copper layers, 152.4 x 101.5 mm, 106 parts (26 on the bottom side), 136 nets.

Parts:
C1, C14: >100uF; E5-10,5
C2, C3, C4, C8, C10, C12: 1uF; C1206
C5, C6, C7, C9, C11, C13: 10uF; C1206@1
D1, D4, D7, D10, D13, D16: CGRM4001-G; SOD-123_MINI-SMA
D2, D3, D5, D6, D8, D9, D11, D12, D14, D15, D17, D18: SMB
E$1, E$2: STACK-CONN-WIDEPITCH
P1, P2, P3, P4, P5, P6, P7, P8, P9, P10, P11: MOLEX_MINIFIT_JR_3CKT; 3CKT_MINIFIT_JR
Q1, Q2, Q3, Q4, Q5, Q6, Q7, Q8, Q9, Q10, Q11, Q12: IPB70N04S3; D-PAK_TO252AA
R1, R2, R3, R4, R5, R6: 1.5k; R2010
R7: R1206
SJ1, SJ2, SJ3, SJ4, SJ5, SJ6, SJ7, SJ8, SJ9, SJ10, SJ11, SJ12, SJ13, SJ14, SJ15, SJ16, SJ17, SJ18, SJ19, SJ21, SJ22, SJ23, SJ24, SJ25, SJ26, SJ27, SJ28, SJ29, SJ30, SJ31, SJ32, SJ33, SJ34, SJ35, SJ36, SJ37: SJ
U1, U2, U3, U4, U5, U6: LT1160CS; SOIC14

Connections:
+12V: C5.1, C6.1, C7.1, C9.1, C11.1, C13.1, D1.A, D4.A, D7.A, D10.A, D13.A, D16.A, P10.3, U1.1, U1.10, U2.1, U2.10, U3.1, U3.10, U4.1, U4.10, U5.1, U5.10, U6.1, U6.10
+24V: C1.+, C14.+, P11.3, R7.2
AGND: C1.-, C14.-, D3.A, D6.A, D9.A, D12.A, D15.A, D18.A, P1.3, P3.3, P4.3, P6.3, P7.3, P9.3, P11.2, Q2.3, Q4.3, Q6.3, Q8.3, Q10.3, Q12.3, R1.1, R2.1, R3.1, R4.1, R5.1, R6.1, R7.1, U1.6, U2.6, U3.6, U4.6, U5.6, U6.6
GND: C5.2, C6.2, C7.2, C9.2, C11.2, C13.2, E$1.A1, E$1.A2, E$1.A7, E$1.A8, E$1.A15, E$1.A22, E$1.A29, E$1.A36, E$1.A43, E$1.A50, E$1.A57, E$1.A60, E$1.B1, E$1.B2, E$1.B7, E$1.B8, E$1.B15, E$1.B22, E$1.B29, E$1.B36, E$1.B43, E$1.B50, E$1.B57, E$1.B60, E$2.A1, E$2.A4, E$2.A11, E$2.A18, E$2.A25, E$2.A32, E$2.A39, E$2.A46, E$2.A53, E$2.A54, E$2.A60, E$2.B1, E$2.B4, E$2.B11, E$2.B18, E$2.B25, E$2.B32, E$2.B39, E$2.B46, E$2.B53, E$2.B54, E$2.B59, E$2.B60, U1.5, U2.5, U3.5, U4.5, U5.5, U6.5
unnamed: C2.1, D1.C, U1.14
unnamed: SJ5.2, SJ6.2, SJ7.2, U3.3
unnamed: C3.1, D7.C, U3.14
unnamed: SJ2.2, SJ3.2, SJ4.2, U3.2
unnamed: SJ17.2, SJ18.2, U1.3
unnamed: Q1.1, U1.12, U1.13
unnamed: Q5.1, U3.12, U3.13
unnamed: C8.1, D10.C, U4.14
unnamed: Q8.1, U4.8, U4.9
unnamed: SJ21.2, U4.2
unnamed: SJ22.2, SJ23.2, SJ24.2, U4.3
unnamed: Q7.1, U4.12, U4.13
unnamed: C10.1, D13.C, U5.14
unnamed: SJ25.2, SJ26.2, SJ27.2, U5.3
unnamed: Q9.1, U5.12, U5.13
unnamed: C12.1, D16.C, U6.14
unnamed: Q12.1, U6.8, U6.9
unnamed: SJ31.2, SJ32.2, U6.3
unnamed: Q11.1, U6.12, U6.13
unnamed: C4.1, D4.C, U2.14
unnamed: Q4.1, U2.8, U2.9
unnamed: SJ9.2, SJ10.2, U2.2
unnamed: SJ12.2, SJ13.2, SJ14.2, U2.3
unnamed: Q3.1, U2.12, U2.13
unnamed: SJ1.2, SJ8.2, SJ15.2, U1.2
OUTA: C2.2, D2.A, D3.C, P1.1, P2.1, Q1.3, Q2.4, R1.2, U1.11
OUTA1: C3.2, D8.A, D9.C, P4.1, P5.1, Q5.3, Q6.4, R3.2, U3.11
OUTA2: C10.2, D14.A, D15.C, P7.1, P8.1, Q9.3, Q10.4, R5.2, U5.11
OUTB: C4.2, D5.A, D6.C, P2.2, P3.1, Q3.3, Q4.4, R2.2, U2.11
OUTB1: C8.2, D11.A, D12.C, P5.2, P6.1, Q7.3, Q8.4, R4.2, U4.11
OUTB2: C12.2, D17.A, D18.C, P8.2, P9.1, Q11.3, Q12.4, R6.2, U6.11
S$5: E$1.B55, E$2.B6, SJ7.1
S$6: Q2.1, U1.8, U1.9
S$11: Q6.1, U3.8, U3.9
S$12: E$1.B53, E$2.B8, SJ6.1
S$17: Q10.1, U5.8, U5.9
S$18: E$1.B51, E$2.B10, SJ5.1
S$19: E$1.B48, E$2.B13, SJ14.1
S$20: E$1.B46, E$2.B15, SJ13.1
S$21: E$1.B44, E$2.B17, SJ12.1
S$22: E$1.B41, E$2.B20, SJ18.1
S$23: E$1.B39, E$2.B22, SJ17.1
S$24: E$1.B37, E$2.B24
S$25: E$1.B34, E$2.B27, SJ33.1
S$26: E$1.B32, E$2.B29, SJ32.1
S$27: E$1.B30, E$2.B31, SJ31.1
S$28: E$1.B27, E$2.B34, SJ27.1
S$29: E$1.B25, E$2.B36, SJ26.1
S$30: E$1.B23, E$2.B38, SJ25.1
S$31: E$1.B20, E$2.B41, SJ24.1
S$32: E$1.B18, E$2.B43, SJ23.1
S$33: E$1.B16, E$2.B45, SJ22.1
S$34: E$1.B21, E$2.B40, SJ21.1
S$35: E$1.B19, E$2.B42, SJ19.1
S$36: E$1.B17, E$2.B44, SJ37.1
S$37: E$1.B24, E$2.B37, SJ30.1
S$38: E$1.B26, E$2.B35, SJ29.1
S$39: E$1.B28, E$2.B33, SJ28.1
S$40: E$1.B31, E$2.B30, SJ36.1
S$41: E$1.B33, E$2.B28, SJ35.1
S$42: E$1.B35, E$2.B26, SJ34.1
S$43: E$1.B38, E$2.B23, SJ15.1
S$44: E$1.B40, E$2.B21, SJ8.1
S$45: E$1.B42, E$2.B19, SJ1.1
S$46: E$1.B49, E$2.B12, SJ9.1
S$47: E$1.B47, E$2.B14, SJ10.1
S$48: E$1.B45, E$2.B16, SJ11.1
S$49: E$1.B52, E$2.B9, SJ4.1
S$50: E$1.B54, E$2.B7, SJ3.1
S$51: E$1.B56, E$2.B5, SJ2.1
S$53: SJ34.2, SJ35.2, SJ36.2, U6.2
S$54: SJ28.2, SJ29.2, SJ30.2, U5.2
S$57: E$1.A59, E$2.A2
S$58: E$1.A58, E$2.A3
S$60: E$1.A55, E$2.A6
S$61: E$1.A56, E$2.A5
S$62: E$1.A54, E$2.A7
S$63: E$1.A53, E$2.A8
S$64: E$1.A52, E$2.A9
S$65: E$1.A51, E$2.A10
S$67: E$1.A49, E$2.A12
S$68: E$1.A48, E$2.A13
S$69: E$1.A47, E$2.A14
S$70: E$1.A46, E$2.A15
S$71: E$1.A45, E$2.A16
S$72: E$1.A44, E$2.A17
S$74: E$1.A42, E$2.A19
S$75: E$1.A41, E$2.A20
S$76: E$1.A40, E$2.A21
S$77: E$1.A38, E$2.A23
S$78: E$1.A39, E$2.A22
S$79: E$1.A37, E$2.A24
S$81: E$1.A34, E$2.A27
S$82: E$1.A35, E$2.A26
S$83: E$1.A33, E$2.A28
S$84: E$1.A32, E$2.A29
S$85: E$1.A31, E$2.A30
S$86: E$1.A30, E$2.A31
S$88: E$1.A28, E$2.A33
S$89: E$1.A27, E$2.A34
S$90: E$1.A25, E$2.A36
S$91: E$1.A26, E$2.A35
S$92: E$1.A23, E$2.A38
S$93: E$1.A24, E$2.A37
S$95: E$1.A20, E$2.A41
S$96: E$1.A21, E$2.A40
S$97: E$1.A19, E$2.A42
S$98: E$1.A18, E$2.A43
S$99: E$1.A16, E$2.A45
S$100: E$1.A17, E$2.A44
S$102: E$1.A14, E$2.A47
S$103: E$1.A13, E$2.A48
S$104: E$1.A11, E$2.A50
S$105: E$1.A12, E$2.A49
S$106: E$1.A10, E$2.A51
S$107: E$1.A9, E$2.A52
S$109: E$1.A6, E$2.A55
S$111: E$1.A4, E$2.A57
S$112: E$1.A5, E$2.A56
S$113: E$1.A3, E$2.A58
S$117: E$1.B59, E$2.B2
S$119: E$1.B58, E$2.B3
S$126: E$1.B13, E$2.B48
S$127: E$1.B14, E$2.B47
S$128: E$1.B11, E$2.B50
S$129: E$1.B12, E$2.B49
S$130: E$1.B10, E$2.B51
S$132: E$1.B9, E$2.B52
S$133: E$1.B6, E$2.B55
S$135: E$1.B5, E$2.B56
S$136: E$1.B4, E$2.B57
S$137: E$1.B3, E$2.B58

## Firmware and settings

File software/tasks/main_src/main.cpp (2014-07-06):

#include <stdlib.h>
#include <stdio.h>

#include "mda_vision.h"
#include "mda_tasks.h"

// This is just a program to test proper linking of code in task

#define IMAGE_NAME "../vision/color1.jpg"

int main (int argc, char** argv) {
    IplImage * raw_img = cvLoadImage(IMAGE_NAME);
    IplImage * img = mvCreateImage_Color();

    cvResize (raw_img, img);

    MDA_VISION_MODULE_BASE* gate_module = NULL;
    MDA_VISION_MODULE_BASE* path_module = NULL;
    MDA_VISION_MODULE_BASE* buoy_module = NULL;
    MDA_VISION_MODULE_BASE* goalpost_module = NULL;
    
    gate_module = new MDA_VISION_MODULE_GATE;
    path_module = new MDA_VISION_MODULE_PATH;
    buoy_module = new MDA_VISION_MODULE_BUOY;
    goalpost_module = new MDA_VISION_MODULE_GOALPOST;


    gate_module->filter (img);
    printf ("gate module passed\n");
    path_module->filter (img);
    printf ("path module passed\n");
    buoy_module->filter (img);
    printf ("buoy module passed\n");
    goalpost_module->filter (img);
    printf ("goalpost module passed\n");

    cvWaitKey(500);
    delete gate_module;
    cvWaitKey(500);
    delete path_module;
    cvWaitKey(500);
    delete buoy_module;
    cvWaitKey(500);
    delete goalpost_module;
    cvWaitKey(500);


    cvReleaseImage (&raw_img);
    cvReleaseImage (&img);

    printf ("\nTest PASSED.\n");
    return 0;
}

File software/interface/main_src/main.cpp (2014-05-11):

/*
* Main file that get compiled as the aquatux executable
*   Pass in an argument specifying what settings file to use to configure what the inputs and outputs should be.
*   If no argument is passed in, use the default settings file (default_aquatux.csv).
*   The argument is used to construct an AquaTux object (see AquaTux.h for more details).
*/

#include "AquaTux.h"

int main(int argc, char **argv)
{
  if (argc > 1) {
    AquaTux at = AquaTux(argv[1]);
    at.work();
  } else {
    AquaTux at = AquaTux("default_aquatux.csv");
    at.work();
  }

  return 0;
}

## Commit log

2014-05-19 Removes mvShaps.h and mvShapes.cpp
    [AdaptiveFilter3_settings.csv, Rect_settings.csv, camera_range_test_settings.csv]
2014-05-19 Removes extra settings file
    [AdvancedCircles_settings.csv]
2014-06-29 renamed frame task files to goalpost task files
    [vision_goalpost_settings.csv]
2014-06-29 more renaming of frame task to goalpost task
2014-06-29 ahhhhhh namesss
    [hacks.csv, sim.csv]
2014-07-06 Testing committing from my computer - added a folder for SONAR Verilog code.
2014-07-06 Embedded 2013 2014 Code and Documentation
    [SPI registers.xlsx]
2014-07-06 (INCOMPLETE) changes to compile aquatux properly
    [vision_buoy_settings_new.csv, vision_test_settings.csv]
2014-07-06 Removed some aquatux setting files
    [aquatux_video_test.csv, aquatux_webcam_test.csv]
2014-07-06 added debug levels, changed setting files, fixed debugging for contour and path module
    [vision_buoy_settings_new.csv, vision_path_settings.csv]
2014-07-10 Changes match_circle to new debug and params infrastructure
    [HSVFilter_settings.csv, HoughLines_settings.csv, vision_path_settings.csv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]
2014-07-29 fixed compilation issue that fixed ritchie's compile but broke everyone else's, and added missing settings reqd for match_rectangle to several task settings
    [vision_buoy_settings_new.csv, vision_gate_settings.csv, vision_goalpost_settings.csv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]
2014-07-30 added temp print statements
    [vision_path_settings.csv]
